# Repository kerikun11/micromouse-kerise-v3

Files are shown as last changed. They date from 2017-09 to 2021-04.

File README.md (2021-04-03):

# MicroMouse KERISE v3

ハーフサイズマイクロマウス

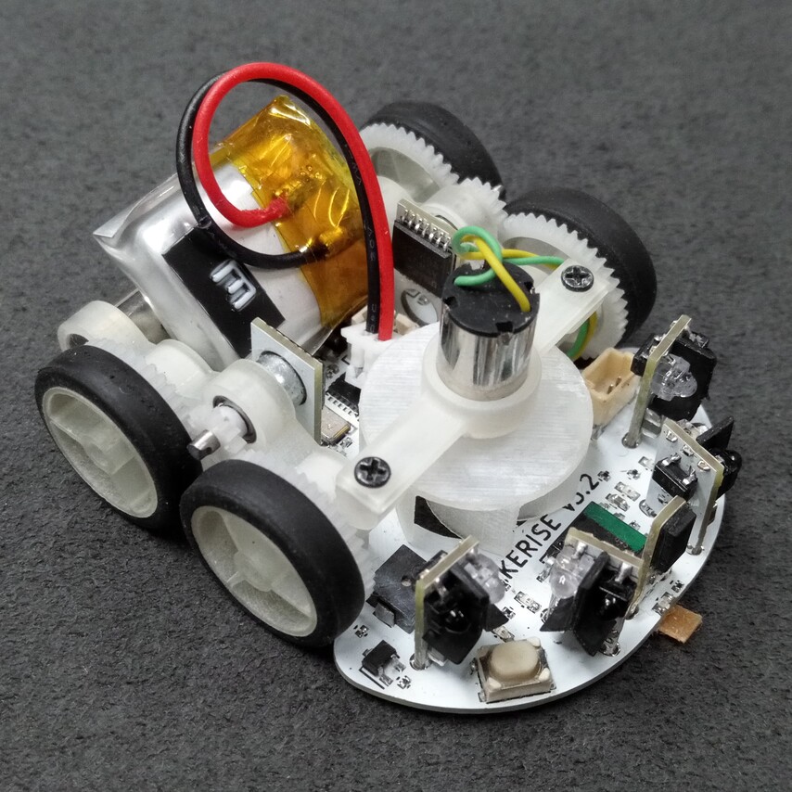
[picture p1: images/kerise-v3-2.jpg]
KERISE v3


## 戦績

- 第38回全日本マイクロマウス大会2017
  - ハーフサイズ競技エキスパートクラス予選13位
  - ハーフサイズ競技エキスパートクラス決勝13位
  - ハーフサイズ競技エキスパートクラス特別賞

## スペック

| 部品 | 型番 | 備考 |
| :--- | :--- | :--- |
| モーター | 不明 | 直径6mm 長さ10mm コアレスモーター |
| エンコーダ | AS5048A | 4096パルス 磁気式 |
| マイコン | ESP32-D0WD  | 240MHz dual core |
| 赤外線LED | VSMB294008G | 波長940mm |
| フォトダイオード | VEMD2020X01 | 波長940nm |
| モータードライバ | DRV8835 | 最大電流1.5A x 2ch |
| 6軸センサ | ICM-20602 | 3軸ジャイロ+3軸加速度 |
| バッテリー | 不明 | 3.7V 25C 100mAh 1S |

## 回路設計

- KiCad

## 開発環境

- ESP-IDF

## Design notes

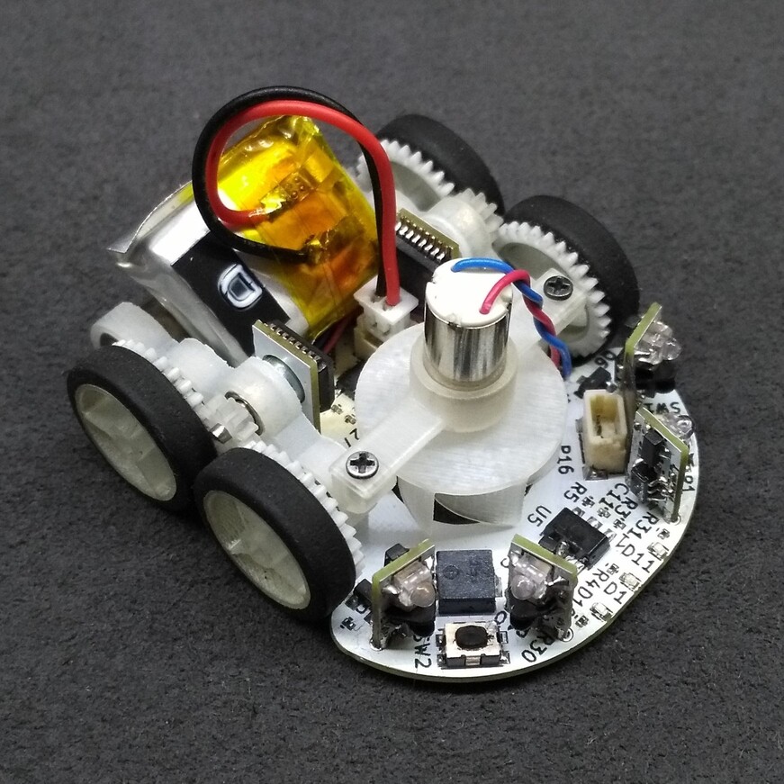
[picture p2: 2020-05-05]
images/kerise-v3-1.jpg

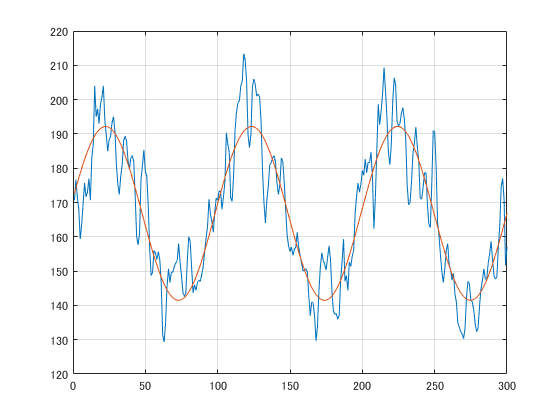
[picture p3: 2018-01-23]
matlab/fit.png

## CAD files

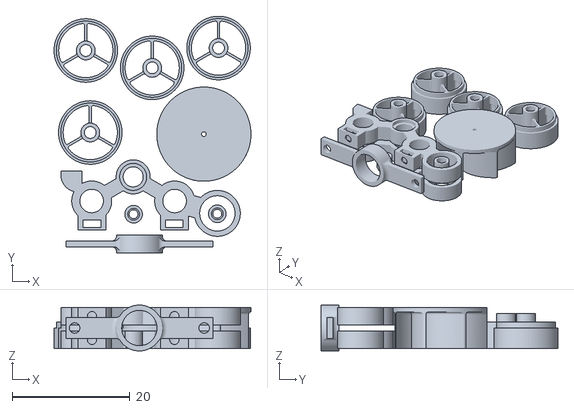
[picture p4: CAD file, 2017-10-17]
fusion360/print/main v1.stl
33.5 x 40.2 x 7.80

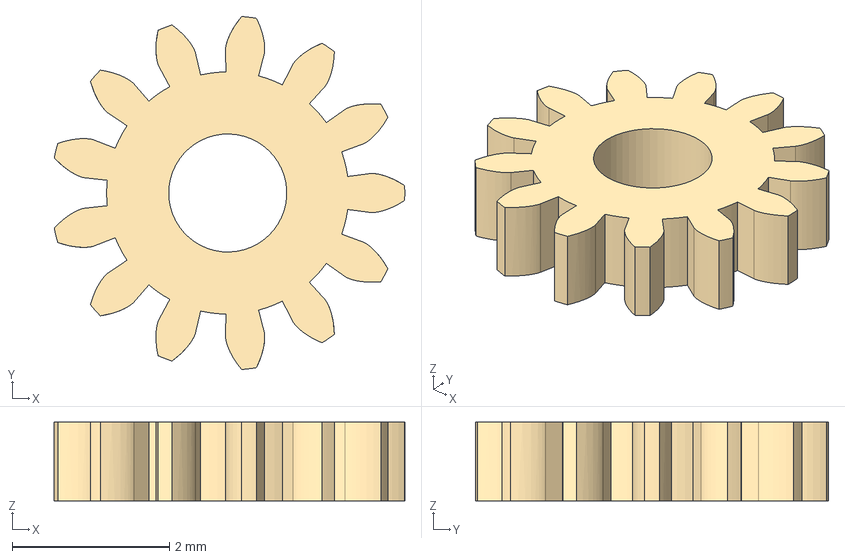
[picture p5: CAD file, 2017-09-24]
fusion360/gear/13.stp
4.46 x 4.49 x 1.00 mm

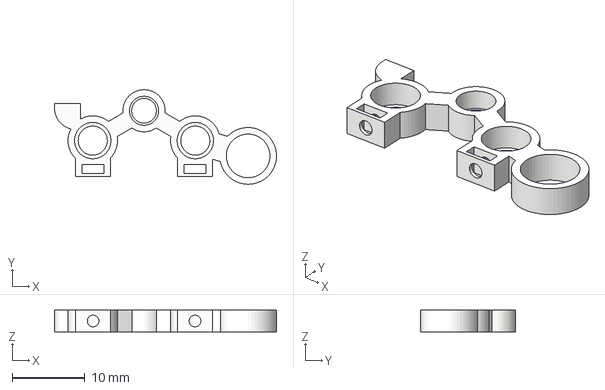
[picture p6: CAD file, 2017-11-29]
fusion360/parts/mounter v11.step
30.5 x 13.0 x 3.00 mm

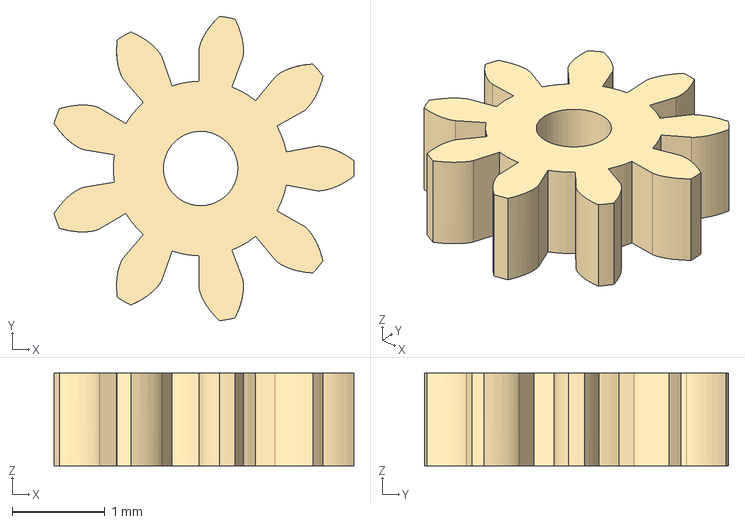
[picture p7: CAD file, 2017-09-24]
fusion360/gear/9.stp
3.23 x 3.28 x 1.00 mm

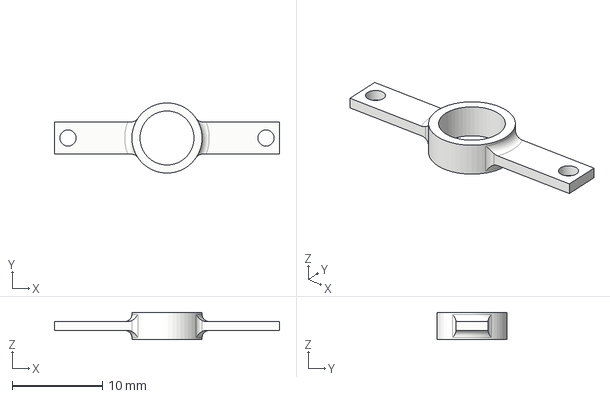
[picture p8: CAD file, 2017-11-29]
fusion360/parts/fan-mounter v1.step
25.0 x 7.80 x 3.00 mm

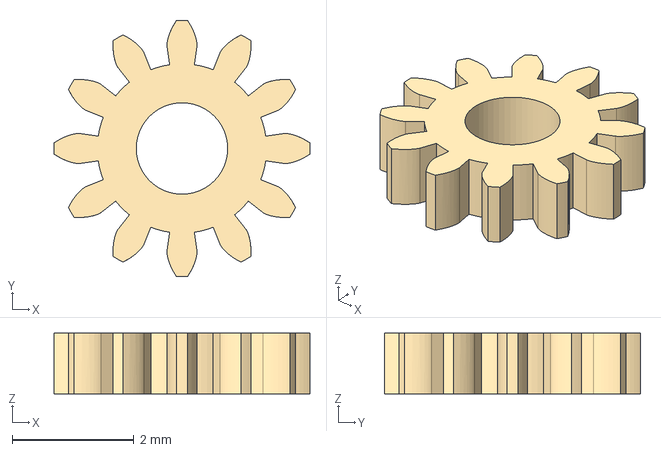
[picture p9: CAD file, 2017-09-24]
fusion360/gear/12.stp
4.20 x 4.20 x 1.00 mm

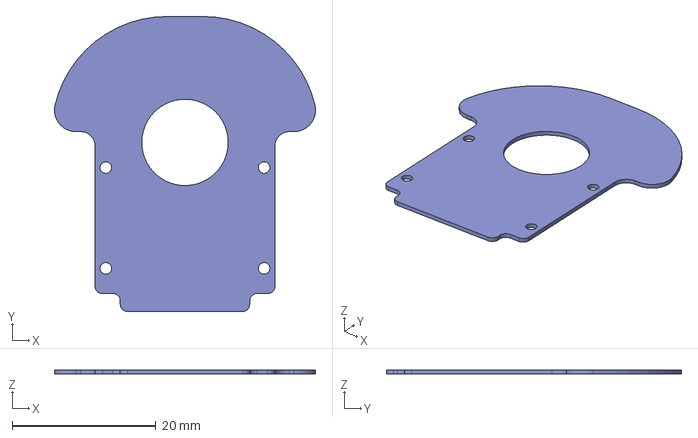
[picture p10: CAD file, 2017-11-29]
fusion360/parts/board v2.step
36.3 x 41.0 x 0.6 mm

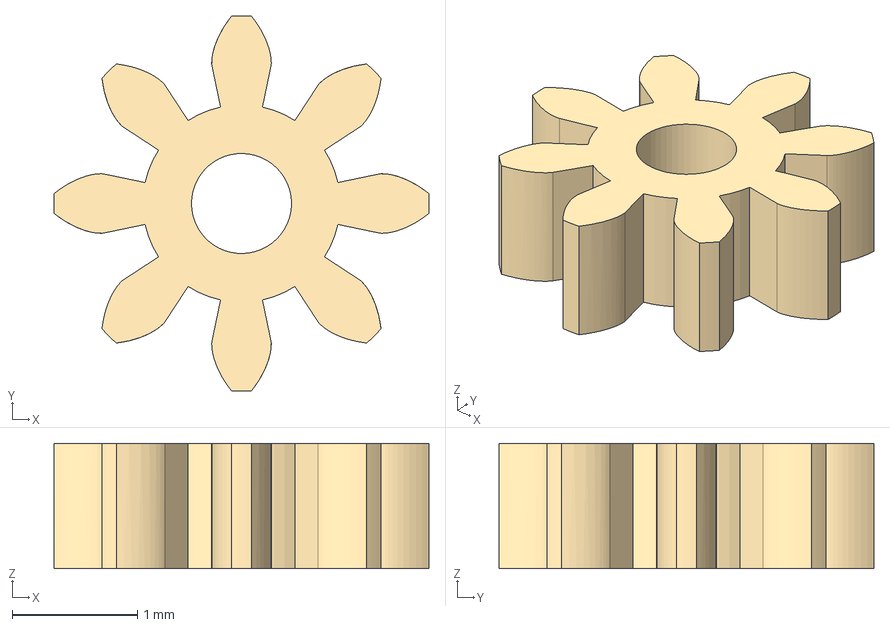
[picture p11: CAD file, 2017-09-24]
fusion360/gear/8.stp
3.00 x 3.00 x 1.00 mm

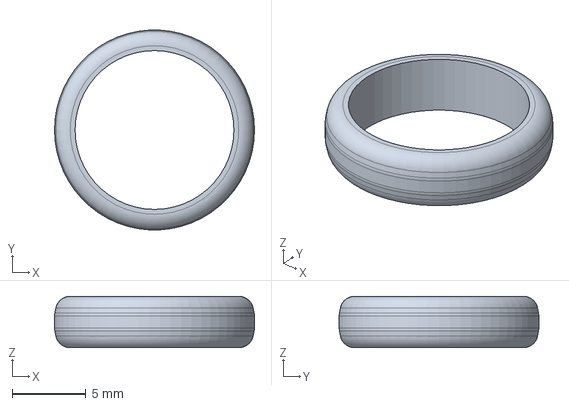
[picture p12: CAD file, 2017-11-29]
fusion360/parts/tire v1.step
13.6 x 13.6 x 3.50 mm

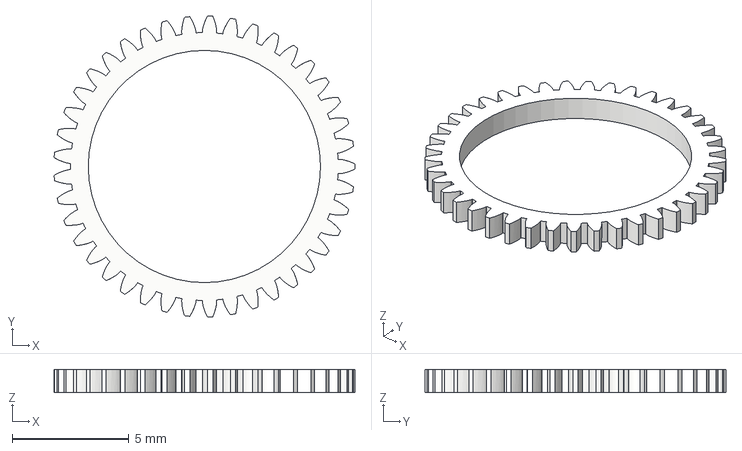
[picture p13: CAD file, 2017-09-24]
fusion360/gear/41.stp
12.9 x 12.9 x 1.00 mm

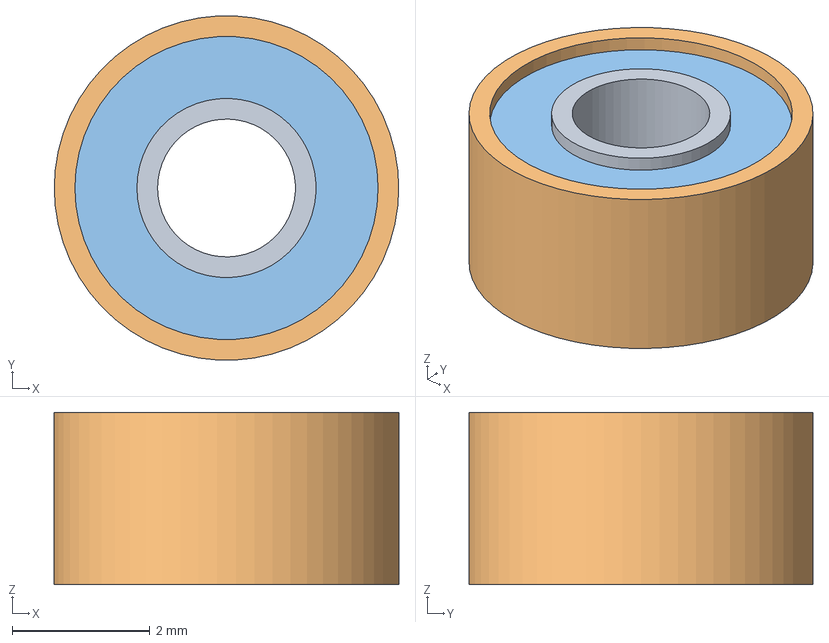
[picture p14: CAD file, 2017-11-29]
fusion360/parts/bearing_2_5_2.5 v1.step
5.00 x 4.99 x 2.50 mm

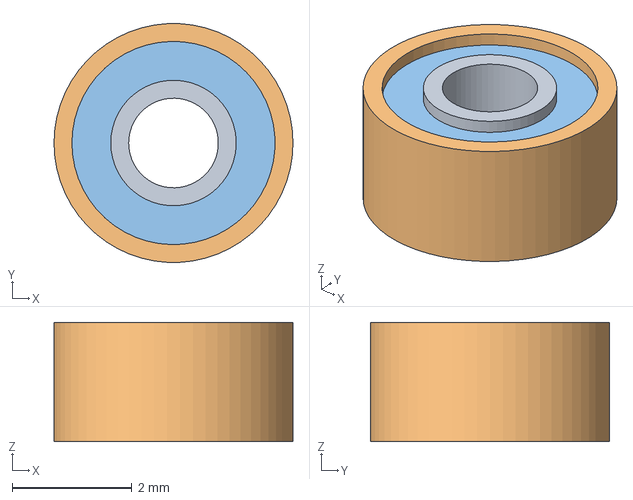
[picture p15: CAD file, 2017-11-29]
fusion360/parts/bearing_1.5_4_2 v1.step
4.00 x 3.99 x 2.00 mm

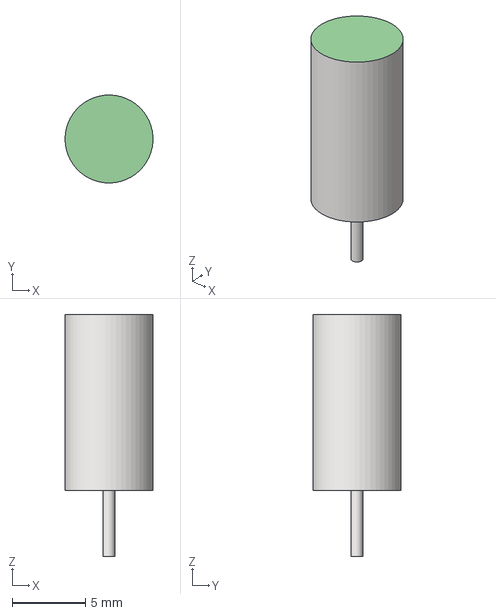
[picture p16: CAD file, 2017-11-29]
fusion360/parts/motor v1.step
5.99 x 6.00 x 16.5 mm

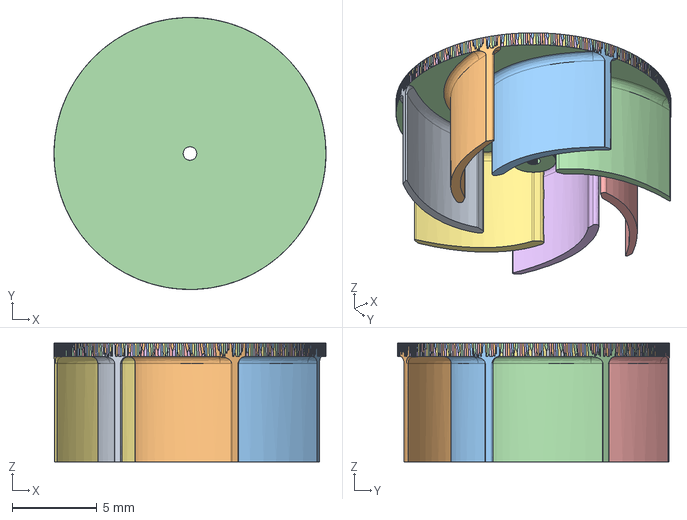
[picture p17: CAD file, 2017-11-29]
fusion360/parts/fan6 v1.step
16.0 x 16.0 x 7.00 mm

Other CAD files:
fusion360/parts/wheel v1.step
fusion360/parts/gear-pinion-9 v1.step
fusion360/parts/magnet-mounter v1.step
fusion360/parts/gear-wheel-41 v3.step
fusion360/gear/12.dxf
fusion360/gear/13.dxf
fusion360/gear/41.dxf
fusion360/gear/8.dxf
fusion360/gear/9.dxf
fusion360/parts/bearing_1.5_4_2 v1.f3d
fusion360/parts/bearing_2_5_2.5 v1.f3d
fusion360/parts/board v2.f3d
fusion360/parts/fan-mounter v1.f3d
fusion360/parts/fan6 v1.f3d
fusion360/parts/gear-encoder-13 v1.f3d
fusion360/parts/gear-encoder-13 v1.step
fusion360/parts/gear-pinion-9 v1.f3d
fusion360/parts/gear-wheel-41 v3.f3d
fusion360/parts/magnet-mounter v1.f3d
fusion360/parts/motor v1.f3d
fusion360/parts/mounter v11.f3d
fusion360/parts/tire v1.f3d
fusion360/parts/wheel v1.f3d

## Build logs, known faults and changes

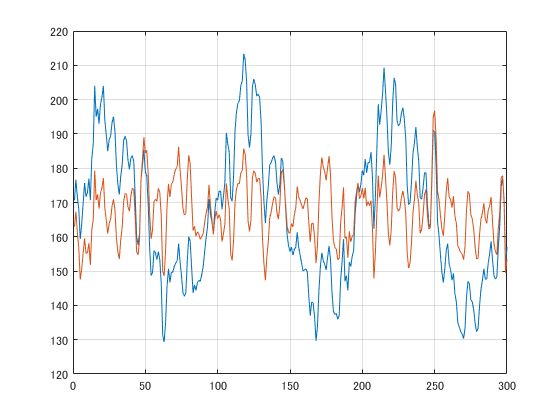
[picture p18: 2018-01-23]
matlab/fix.png

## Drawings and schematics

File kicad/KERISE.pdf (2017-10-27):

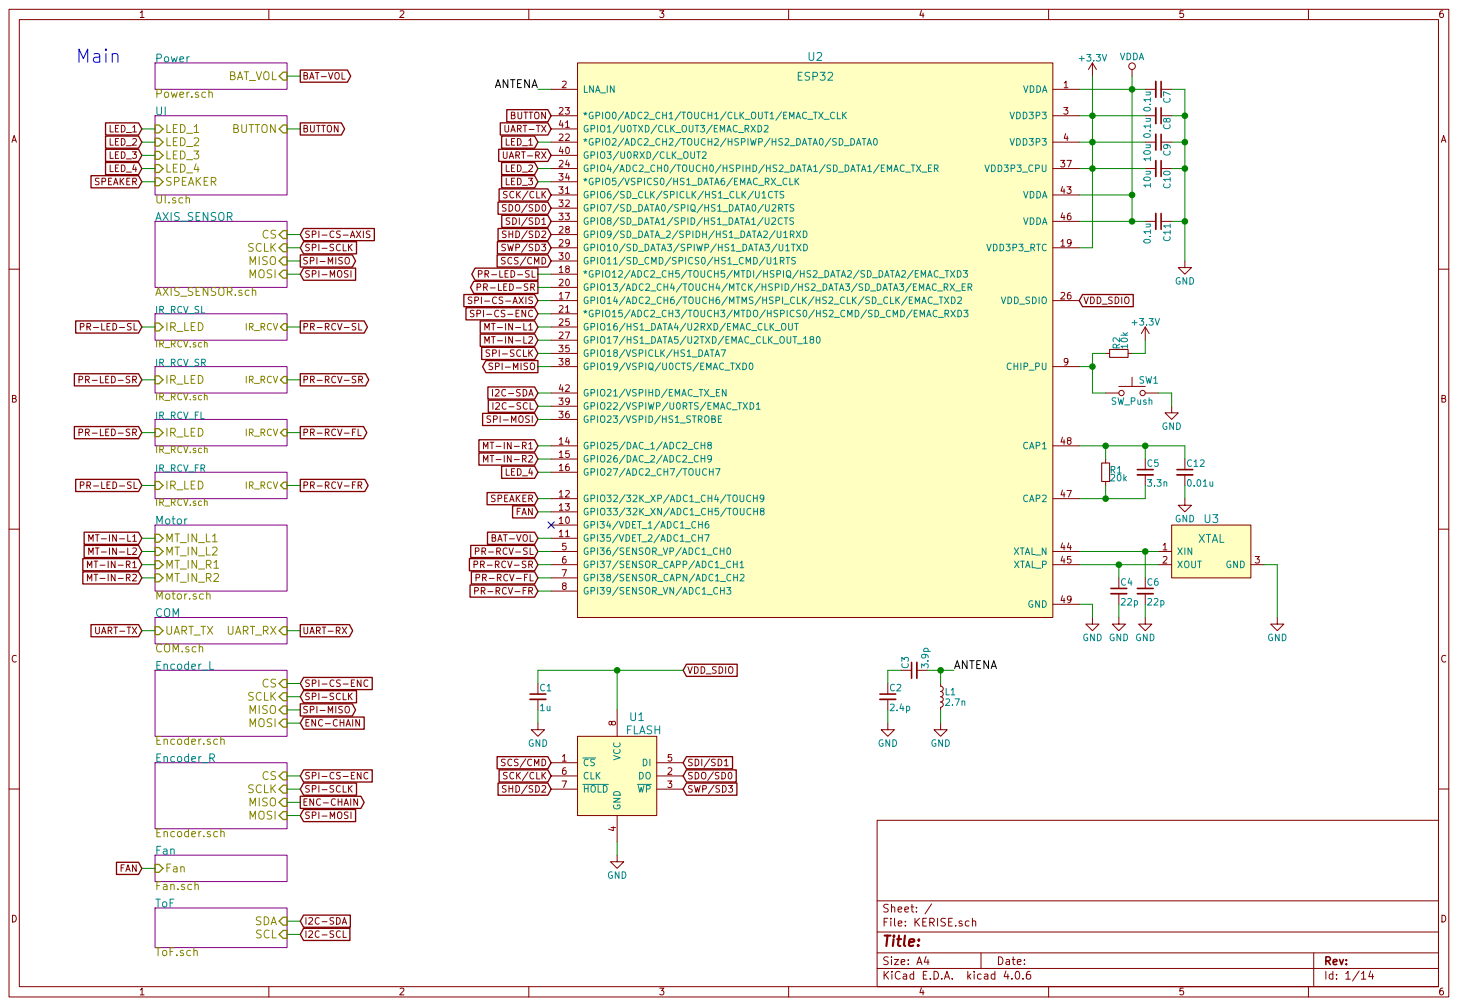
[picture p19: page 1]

BAT-VOL UI UI.sch SPEAKER

UART-TX UART-RX
LED_1

SW1 SW_Push PR-RCV-FL PR-RCV-FR

PR-RCV-FL PR-RCV-FR

UART_TX UART_RX
COM.sch
SPI-MOSI SPI-CS-ENC
SPI-SCLK

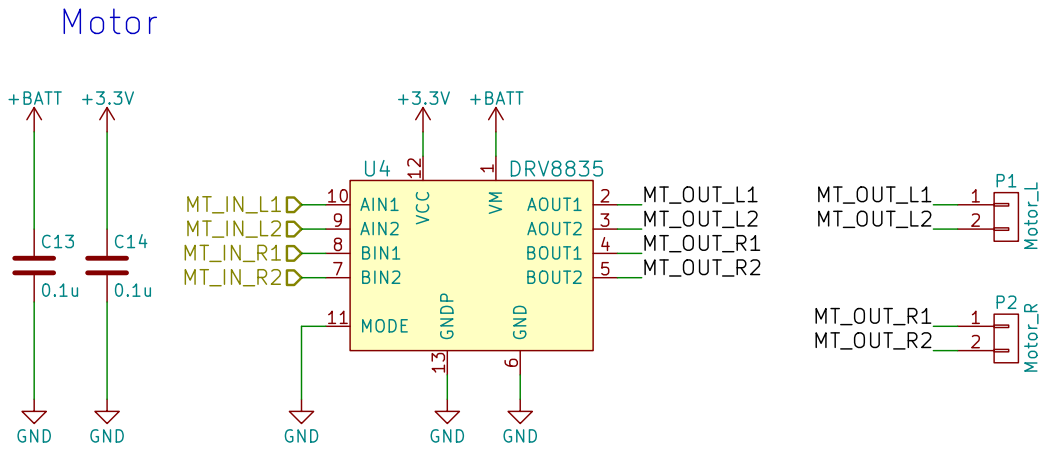
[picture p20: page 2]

6 BIN2 7 BIN1 8 AIN2 9 AIN1 10 MODE 11 VCC 12 GNDP 13 U4 DRV8835 GND GND GND MT_OUT_L1

1 AOUT1 2 AOUT2 3 BOUT1 4 BOUT2 5 GND
Id: 2/14 Title: File: Motor.sch Sheet: /Motor/ VM

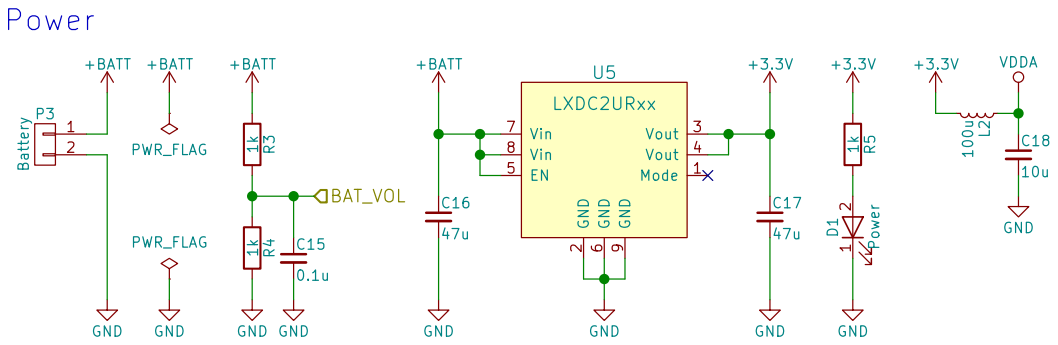
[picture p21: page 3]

2 Vout 3 Vout 4 EN 5 GND

Id: 3/14 Title: File: Power.sch Sheet: /Power/

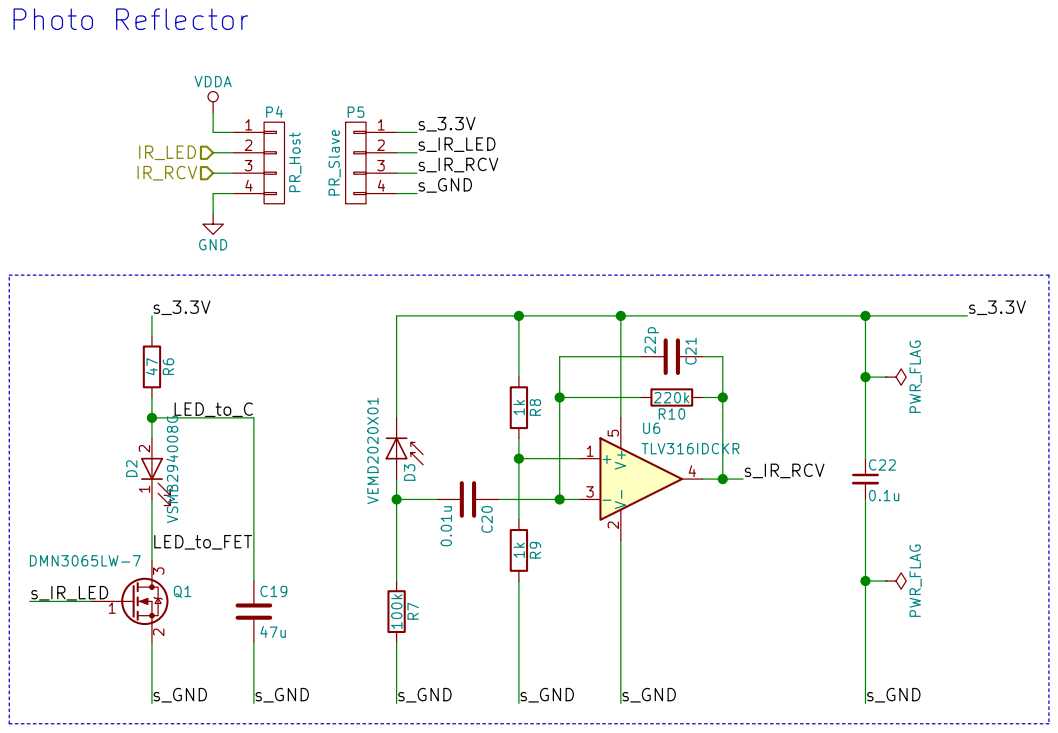
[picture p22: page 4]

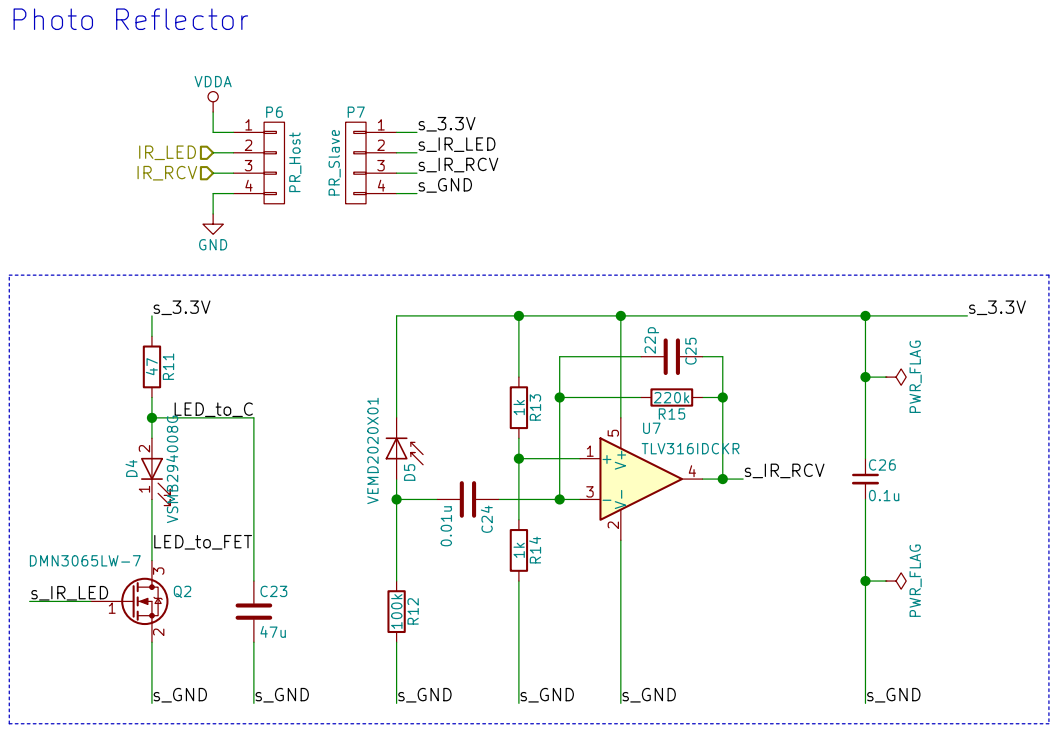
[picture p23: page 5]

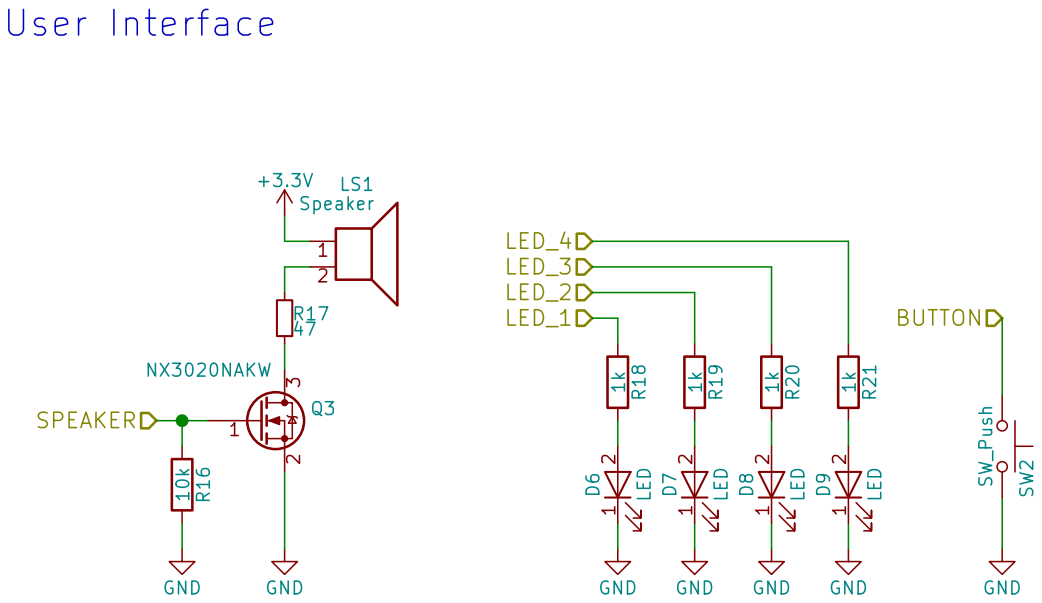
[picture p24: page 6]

Id: 6/14 Title: File: UI.sch Sheet: /UI/

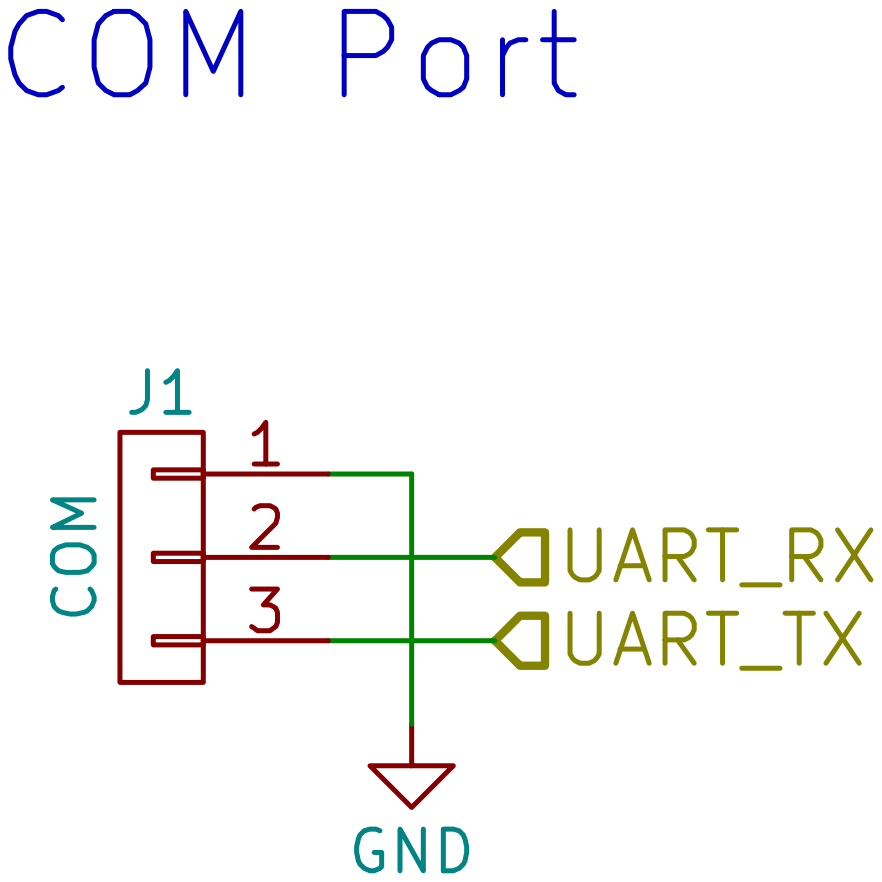
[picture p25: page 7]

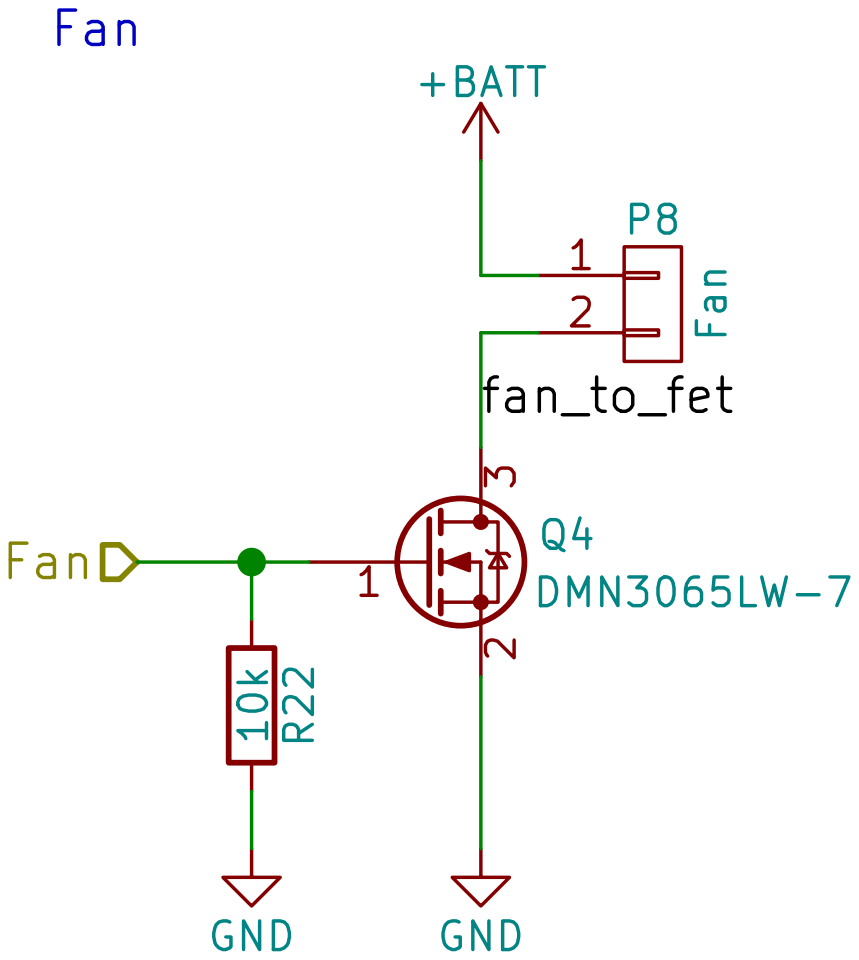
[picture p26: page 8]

Id: 8/14 Title: File: Fan.sch Sheet: /Fan/ 1

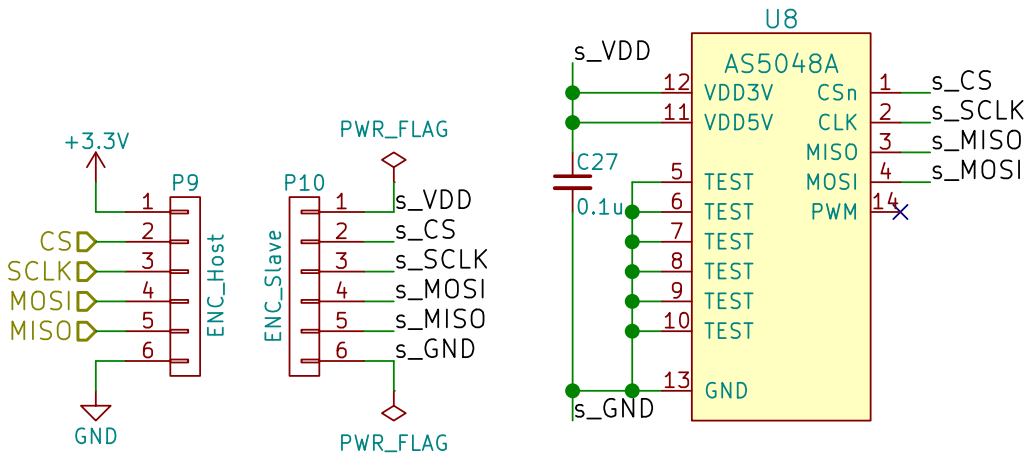
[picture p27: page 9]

Id: 9/14 Title: File: Encoder.sch Sheet: /Encoder_R/ GND CS

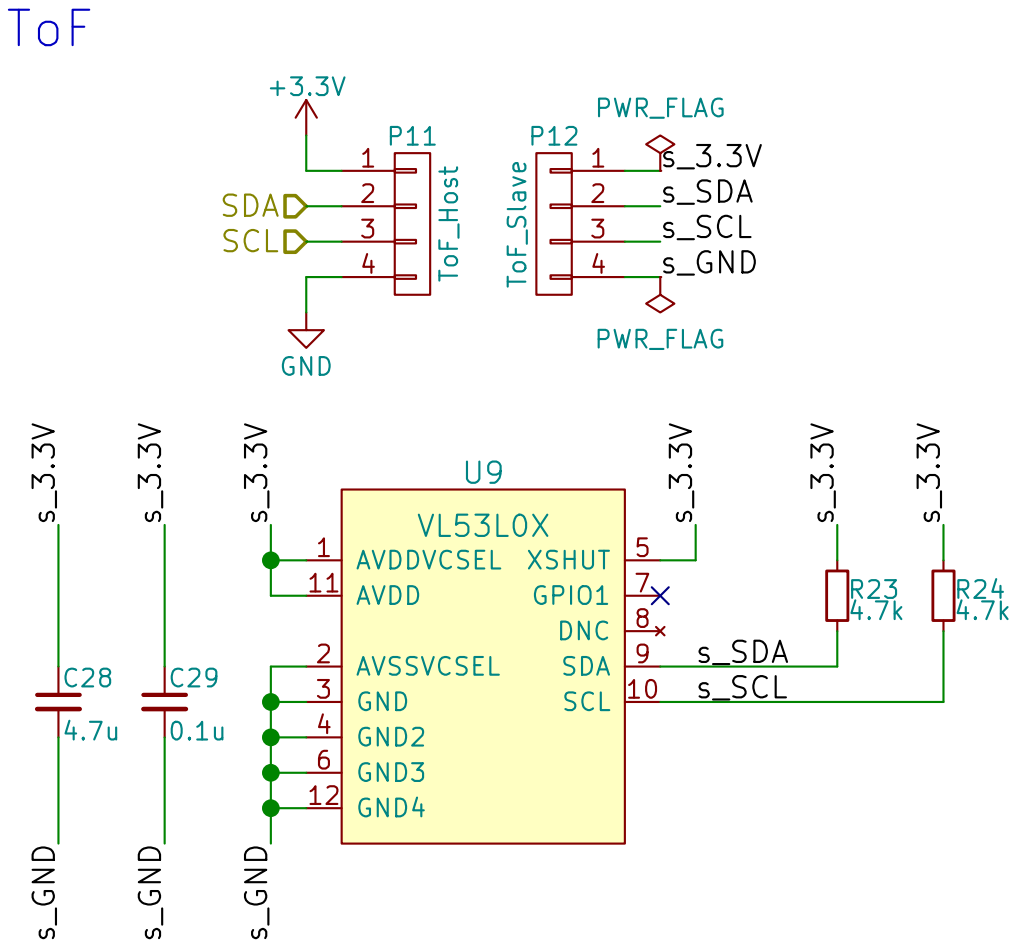
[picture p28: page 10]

Id: 10/14 Title: File: ToF.sch Sheet: /ToF/

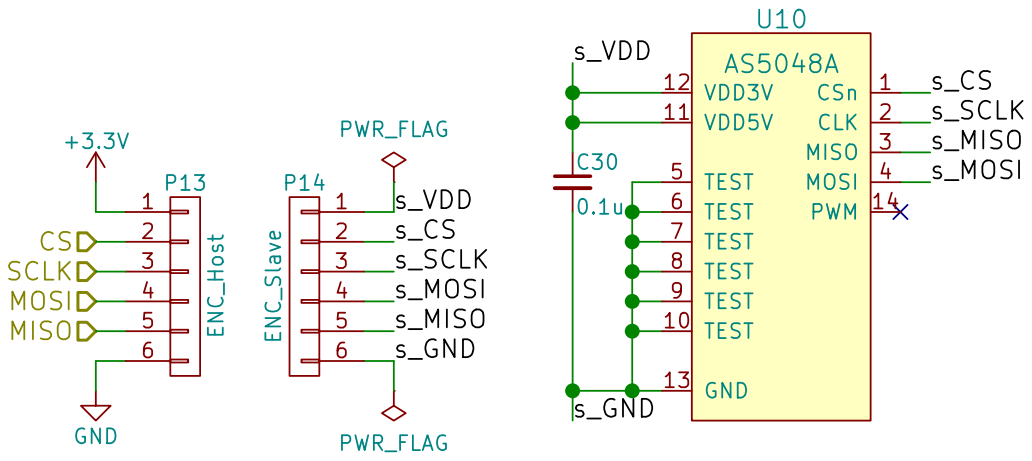
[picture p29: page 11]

Id: 11/14 Title: File: Encoder.sch Sheet: /Encoder_L/ GND CS

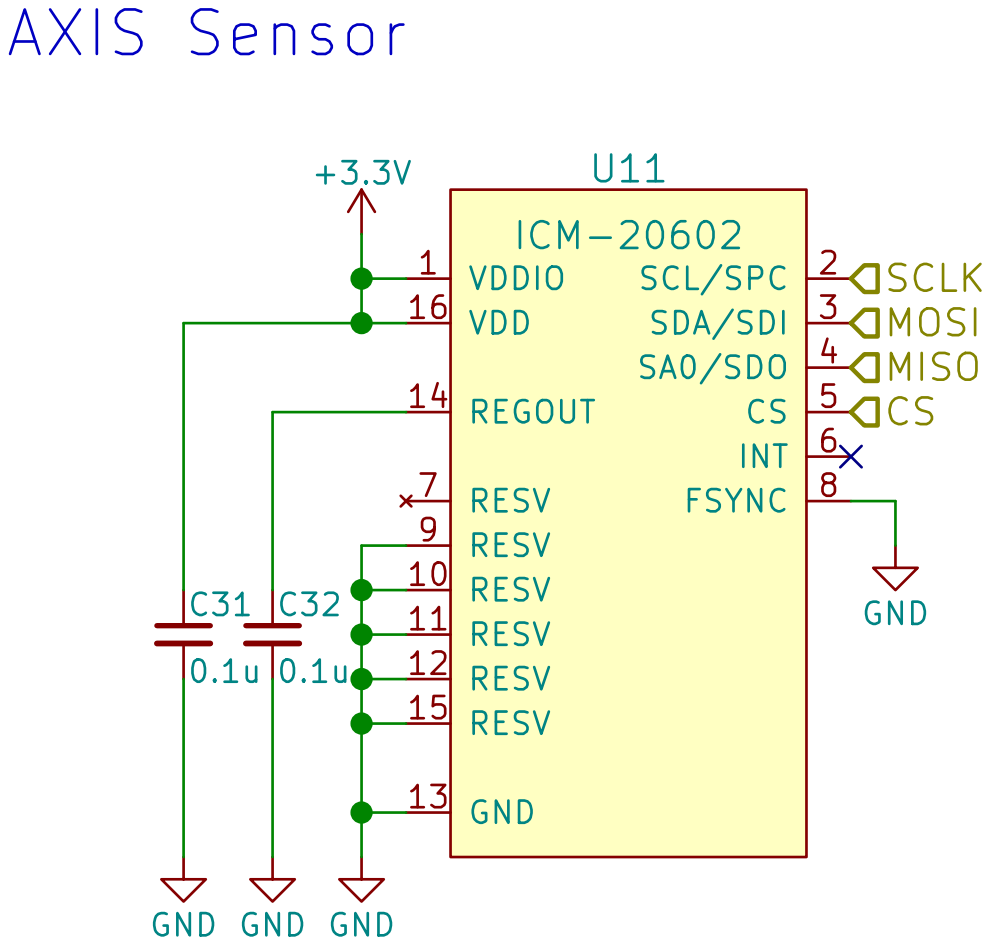
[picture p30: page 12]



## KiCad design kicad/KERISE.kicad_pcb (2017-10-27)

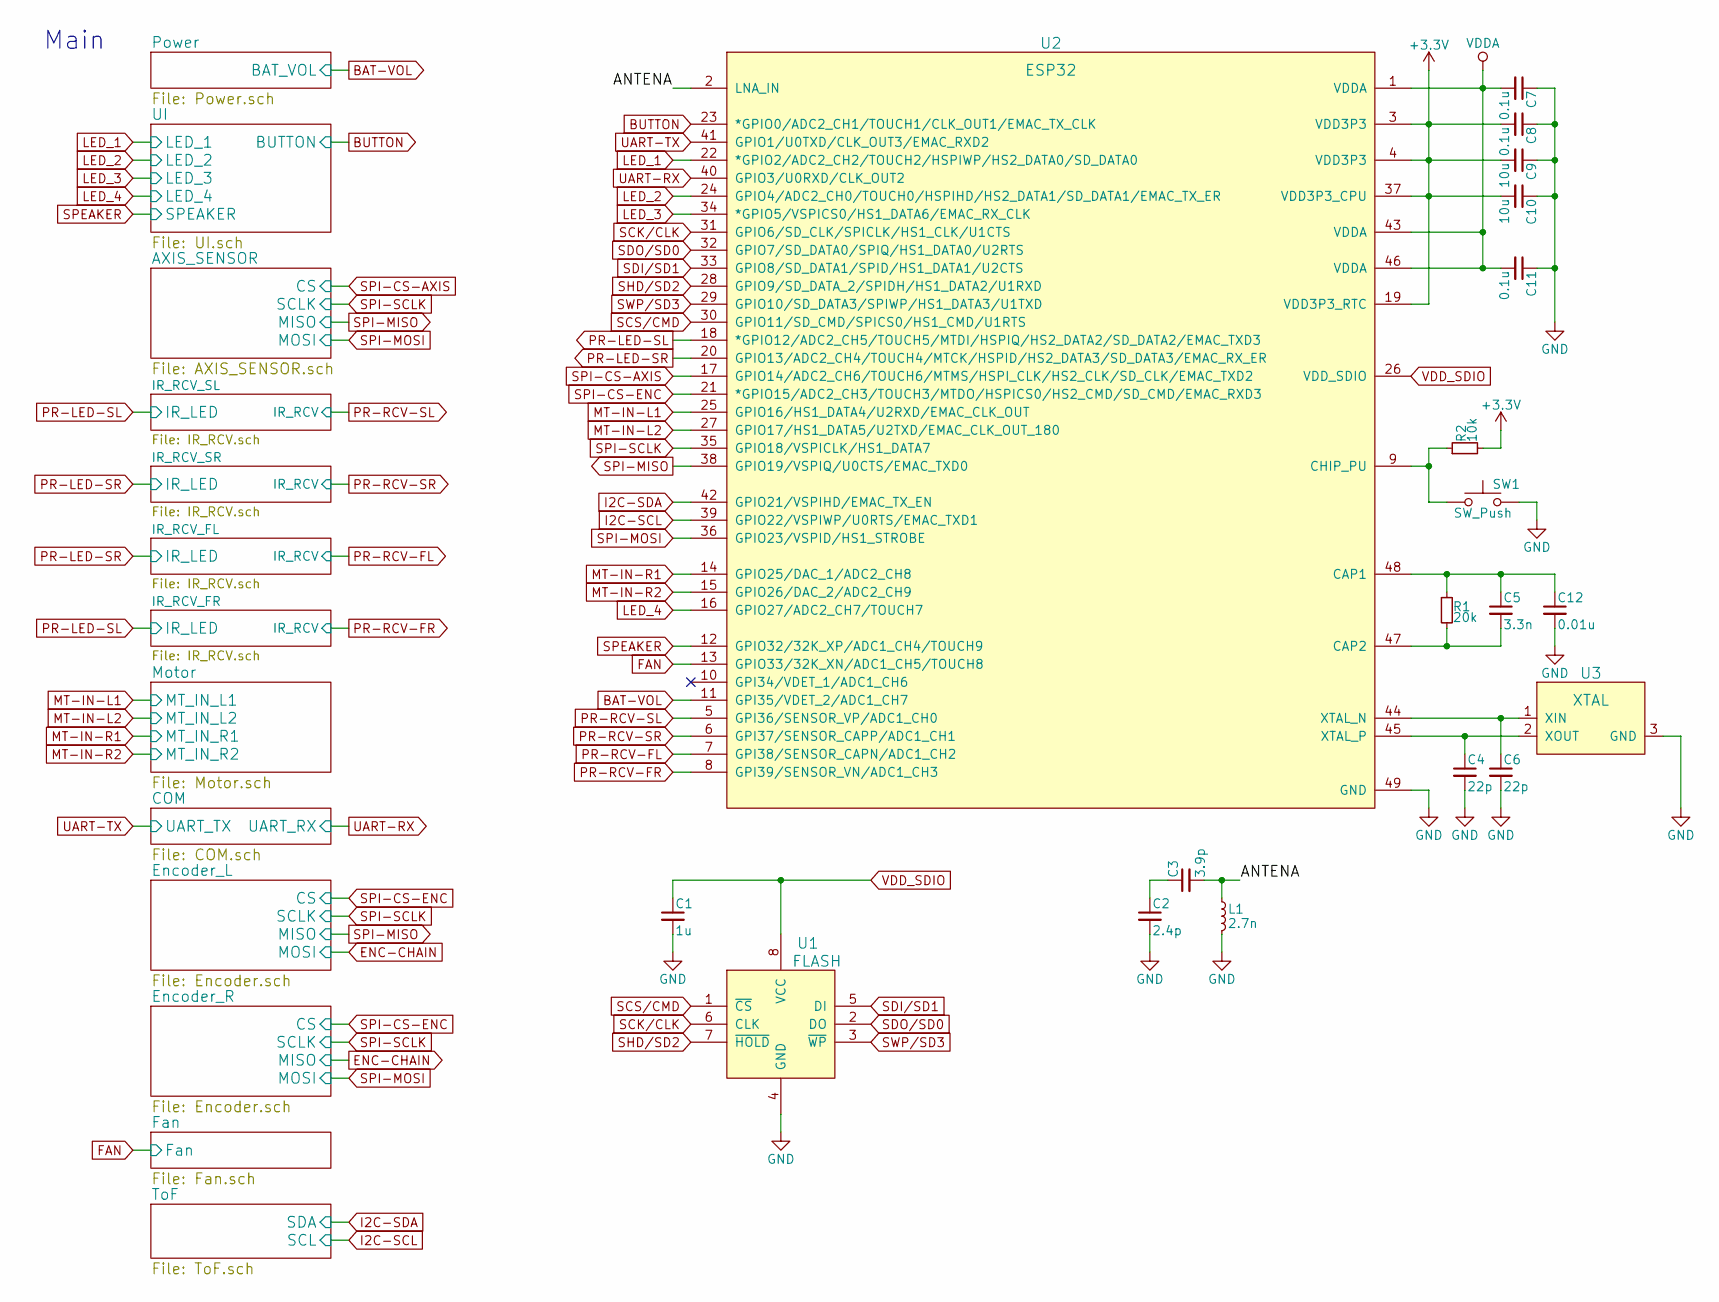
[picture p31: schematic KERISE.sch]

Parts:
C1: 1u; C_0402
C2: 2.4p; C_0201
C3: 3.9p; C_0201
C4, C6: 22p; C_0201
C5: 3.3n; C_0201
C7, C8, C11: 0.1u; C_0201
C9, C10: 10u; C_0402
C12: 0.01u; C_0201
L1: 2.7n; C_0201
R1: 20k; R_0201
R2: 10k; R_0201
SW1: SW_Push; SW_PUSH
U1: FLASH; SOIJ-8_5.3x5.3mm_Pitch1.27mm
U2: ESP32
U3: XTAL; crystal_FA238-TSX3225

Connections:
+3V3: C8.2, C9.2, C10.2, R2.2, U2.3 (VDD3P3), U2.4 (VDD3P3), U2.19 (VDD3P3_RTC), U2.37 (VDD3P3_CPU); also elsewhere on the board
/ANTENA: C3.2, L1.1, U2.2 (LNA_IN)
BAT-VOL: U2.11 (GPI35/VDET_2/ADC1_CH7); also elsewhere on the board
BUTTON: U2.23 (*GPIO0/ADC2_CH1/TOUCH1/CLK_OUT1/EMAC_TX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); also elsewhere on the board
FAN: U2.13 (GPIO33/32K_XN/ADC1_CH5/TOUCH8); also elsewhere on the board
GND: C1.2, C2.2, C4.2, C6.2, C7.1, C8.1, C9.1, C10.1, C11.1, C12.2, L1.2, SW1.2, U1.4 (GND), U2.49 (GND), U3.3 (GND); also elsewhere on the board
I2C-SCL: U2.39 (GPIO22/VSPIWP/U0RTS/EMAC_TXD1); also elsewhere on the board
I2C-SDA: U2.42 (GPIO21/VSPIHD/EMAC_TX_EN); also elsewhere on the board
LED_1: U2.22 (*GPIO2/ADC2_CH2/TOUCH2/HSPIWP/HS2_DATA0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); also elsewhere on the board
LED_2: U2.24 (GPIO4/ADC2_CH0/TOUCH0/HSPIHD/HS2_DATA1/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); also elsewhere on the board
LED_3: U2.34 (*GPIO5/VSPICS0/HS1_DATA6/EMAC_RX_CLK); also elsewhere on the board
LED_4: U2.16 (GPIO27/ADC2_CH7/TOUCH7); also elsewhere on the board
MT-IN-L1: U2.25 (GPIO16/HS1_DATA4/U2RXD/EMAC_CLK_OUT); also elsewhere on the board
MT-IN-L2: U2.27 (GPIO17/HS1_DATA5/U2TXD/EMAC_CLK_OUT_180); also elsewhere on the board
MT-IN-R1: U2.14 (GPIO25/DAC_1/ADC2_CH8); also elsewhere on the board
MT-IN-R2: U2.15 (GPIO26/DAC_2/ADC2_CH9); also elsewhere on the board
unnamed: C2.1, C3.1
unnamed: C4.1, U2.45 (XTAL_P), U3.2 (XOUT)
unnamed: C5.2, R1.2, U2.47 (CAP2)
unnamed: C6.1, U2.44 (XTAL_N), U3.1 (XIN)
unnamed: C5.1, C12.1, R1.1, U2.48 (CAP1)
unnamed: R2.1, SW1.1, U2.9 (CHIP_PU)
PR-LED-SL: U2.18 (*GPIO12/ADC2_CH5/TOUCH5/MTDI/HSPIQ/HS2_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); also elsewhere on the board
PR-LED-SR: U2.20 (GPIO13/ADC2_CH4/TOUCH4/MTCK/HSPID/HS2_D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); also elsewhere on the board
PR-RCV-FL: U2.7 (GPI38/SENSOR_CAPN/ADC1_CH2); also elsewhere on the board
PR-RCV-FR: U2.8 (GPI39/SENSOR_VN/ADC1_CH3); also elsewhere on the board
PR-RCV-SL: U2.5 (GPI36/SENSOR_VP/ADC1_CH0); also elsewhere on the board
PR-RCV-SR: U2.6 (GPI37/SENSOR_CAPP/ADC1_CH1); also elsewhere on the board
SCK/CLK: U1.6 (CLK), U2.31 (GPIO6/SD_CLK/SPICLK/HS1_CLK/U1CTS)
SCS/CMD: U1.1 (~CS), U2.30 (GPIO11/SD_CMD/SPICS0/HS1_CMD/U1RTS)
SDI/SD1: U1.5 (DI), U2.33 (GPIO8/SD_DATA1/SPID/HS1_DATA1/U2CTS)
SDO/SD0: U1.2 (DO), U2.32 (GPIO7/SD_DATA0/SPIQ/HS1_DATA0/U2RTS)
SHD/SD2: U1.7 (~HOLD), U2.28 (GPIO9/SD_DATA_2/SPIDH/HS1_DATA2/U1RXD)
SPEAKER: U2.12 (GPIO32/32K_XP/ADC1_CH4/TOUCH9); also elsewhere on the board
SPI-CS-AXIS: U2.17 (GPIO14/ADC2_CH6/TOUCH6/MTMS/HSPI_CLK/HS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); also elsewhere on the board
SPI-CS-ENC: U2.21 (*GPIO15/ADC2_CH3/TOUCH3/MTDO/HSPICS0/HS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); also elsewhere on the board
SPI-MISO: U2.38 (GPIO19/VSPIQ/U0CTS/EMAC_TXD0); also elsewhere on the board
SPI-MOSI: U2.36 (GPIO23/VSPID/HS1_STROBE); also elsewhere on the board
SPI-SCLK: U2.35 (GPIO18/VSPICLK/HS1_DATA7); also elsewhere on the board
SWP/SD3: U1.3 (~WP), U2.29 (GPIO10/SD_DATA3/SPIWP/HS1_DATA3/U1TXD)
UART-RX: U2.40 (GPIO3/U0RXD/CLK_OUT2); also elsewhere on the board
UART-TX: U2.41 (GPIO1/U0TXD/CLK_OUT3/EMAC_RXD2); also elsewhere on the board
VDDA: C7.2, C11.2, U2.1 (VDDA), U2.43 (VDDA), U2.46 (VDDA); also elsewhere on the board
VDD_SDIO: C1.1, U1.8 (VCC), U2.26 (VDD_SDIO)

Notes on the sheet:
Main

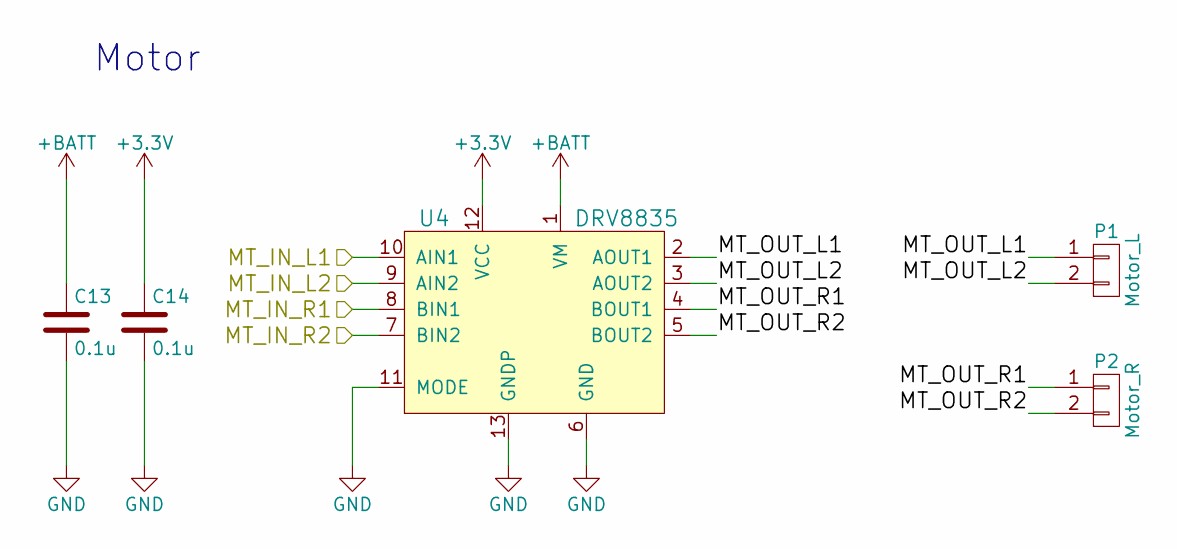
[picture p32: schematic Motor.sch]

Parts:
C13, C14: 0.1u; C_0201
P1: Motor_L; SMD_conn_2
P2: Motor_R; SMD_conn_2
U4: DRV8835

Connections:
+3V3: C14.1, U4.12 (VCC); also elsewhere on the board
+BATT: C13.1, U4.1 (VM); also elsewhere on the board
/Motor/MT_OUT_L1: P1.1, U4.2 (AOUT1)
/Motor/MT_OUT_L2: P1.2, U4.3 (AOUT2)
/Motor/MT_OUT_R1: P2.1, U4.4 (BOUT1)
/Motor/MT_OUT_R2: P2.2, U4.5 (BOUT2)
GND: C13.2, C14.2, U4.6 (GND), U4.11 (MODE), U4.13 (GNDP); also elsewhere on the board
MT-IN-L1: U4.10 (AIN1); also elsewhere on the board
MT-IN-L2: U4.9 (AIN2); also elsewhere on the board
MT-IN-R1: U4.8 (BIN1); also elsewhere on the board
MT-IN-R2: U4.7 (BIN2); also elsewhere on the board

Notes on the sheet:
Motor

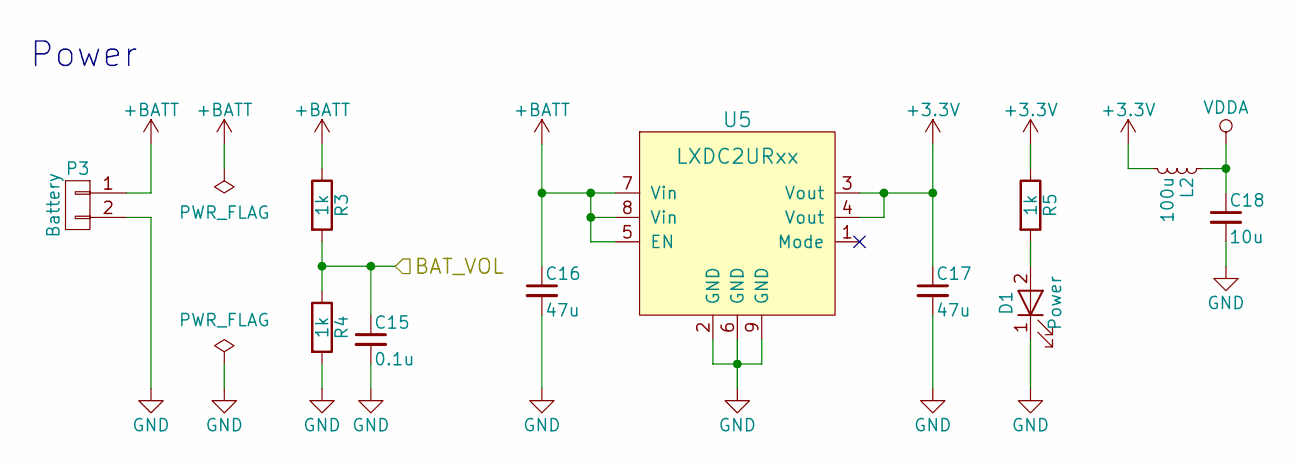
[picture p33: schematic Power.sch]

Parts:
C15: 0.1u; C_0201
C16, C17: 47u; C_0805
C18: 10u; C_0402
D1: Power; LED_0402
L2: 100u; C_0603
P3: Battery; Hirose_DF13-02P-1.25DSA_02x1.25mm_Straight
R3, R4, R5: 1k; R_0201
U5: LXDC2URxx; LXDC2UR

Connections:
+3V3: C17.1, L2.2, R5.1, U5.3 (Vout), U5.4 (Vout); also elsewhere on the board
+BATT: C16.1, P3.1, R3.1, U5.5 (EN), U5.7 (Vin), U5.8 (Vin); also elsewhere on the board
BAT-VOL: C15.1, R3.2, R4.1; also elsewhere on the board
GND: C15.2, C16.2, C17.2, C18.2, D1.1 (K), P3.2, R4.2, U5.2 (GND), U5.6 (GND), U5.9 (GND); also elsewhere on the board
unnamed: D1.2 (A), R5.2
VDDA: C18.1, L2.1; also elsewhere on the board

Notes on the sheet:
Power

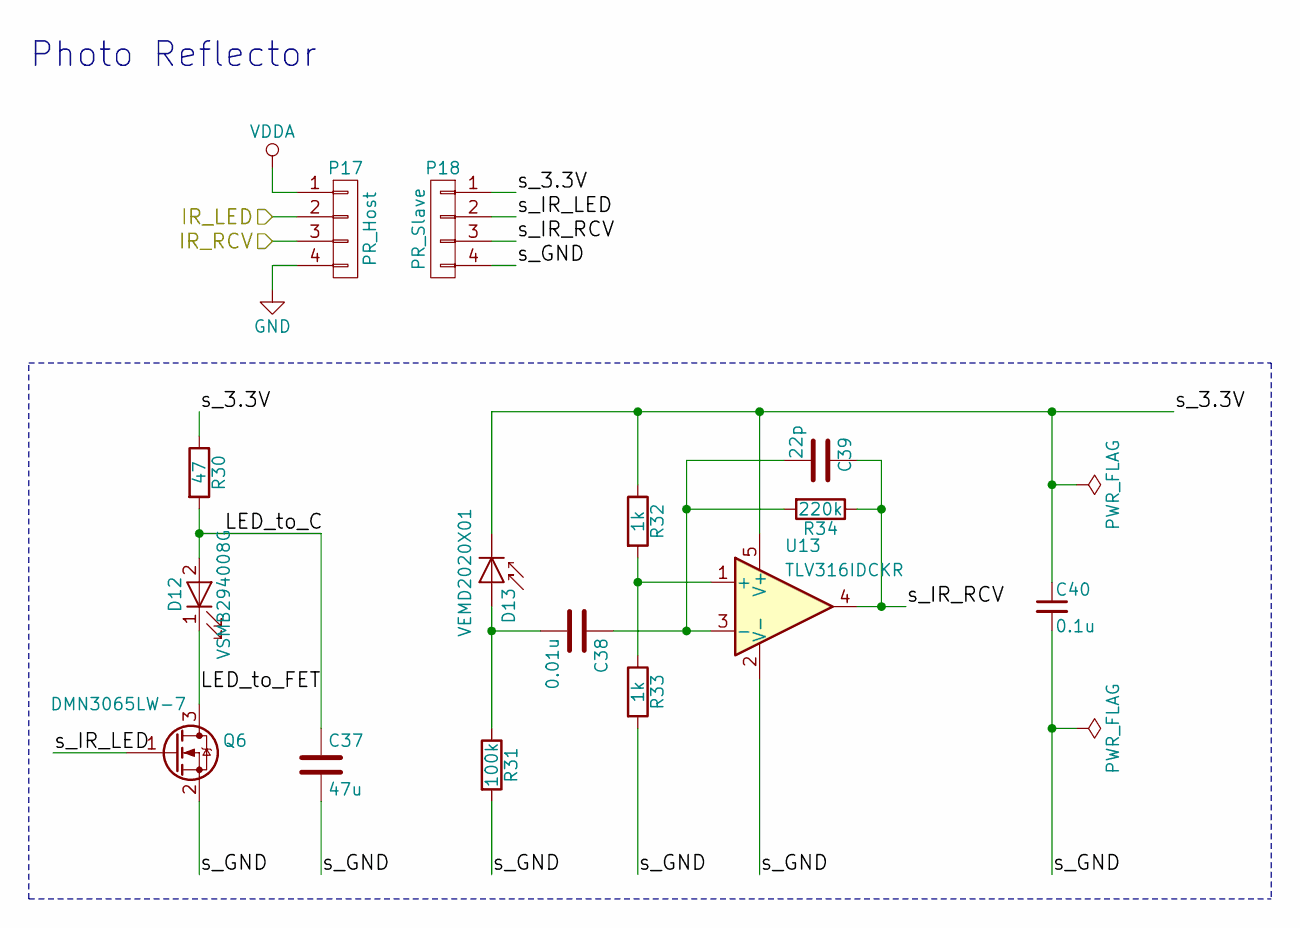
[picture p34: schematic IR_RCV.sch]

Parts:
C19: 47u; C_0805
C20: 0.01u; C_0201
C21: 22p; C_0201
C22: 0.1u; C_0201
D2: VSMB294008G; VISHAY_DIODE
D3: VEMD2020X01; VISHAY_DIODE
P4: PR_Host; STAND_PR_HOST
P5: PR_Slave; STAND_PR_SLAVE
Q1: DMN3065LW-7; SOT-323_SC-70
R6: 47; R_0603
R7: 100k; R_0201
R8, R9: 1k; R_0201
R10: 220k; R_0201
U6: TLV316IDCKR; SOT-353_SC-70-5

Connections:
/IR_RCV_SL/LED_to_C: C19.1, D2.2 (A), R6.2
/IR_RCV_SL/LED_to_FET: D2.1 (K), Q1.3 (D)
/IR_RCV_SL/s_3.3V: C22.1, D3.1 (K), P5.1, R6.1, R8.1, U6.5 (V+)
/IR_RCV_SL/s_GND: C19.2, C22.2, P5.4, Q1.2 (S), R7.2, R9.2, U6.2 (V-)
/IR_RCV_SL/s_IR_LED: P5.2, Q1.1 (G)
/IR_RCV_SL/s_IR_RCV: C21.1, P5.3, R10.1, U6.4
GND: P4.4; also elsewhere on the board
unnamed: C20.1, C21.2, R10.2, U6.3 (-)
unnamed: C20.2, D3.2 (A), R7.1
unnamed: R8.2, R9.1, U6.1 (+)
PR-LED-SL: P4.2; also elsewhere on the board
PR-RCV-SL: P4.3; also elsewhere on the board
VDDA: P4.1; also elsewhere on the board

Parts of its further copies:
C23, C33, C37: 47u; C_0805
C24, C34, C38: 0.01u; C_0201
C25, C35, C39: 22p; C_0201
C26, C36, C40: 0.1u; C_0201
D4, D10, D12: VSMB294008G; VISHAY_DIODE
D5, D11, D13: VEMD2020X01; VISHAY_DIODE
P6, P15, P17: PR_Host; STAND_PR_HOST
P7, P16, P18: PR_Slave; STAND_PR_SLAVE
Q2, Q5, Q6: DMN3065LW-7; SOT-323_SC-70
R11, R25, R30: 47; R_0603
R12, R26, R31: 100k; R_0201
R13, R14, R27, R28, R32, R33: 1k; R_0201
R15, R29, R34: 220k; R_0201
U7, U12, U13: TLV316IDCKR; SOT-353_SC-70-5

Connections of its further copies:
/IR_RCV_FL/LED_to_C: C33.1, D10.2 (A), R25.2
/IR_RCV_FL/LED_to_FET: D10.1 (K), Q5.3 (D)
/IR_RCV_FL/s_3.3V: C36.1, D11.1 (K), P16.1, R25.1, R27.1, U12.5 (V+)
/IR_RCV_FL/s_GND: C33.2, C36.2, P16.4, Q5.2 (S), R26.2, R28.2, U12.2 (V-)
/IR_RCV_FL/s_IR_LED: P16.2, Q5.1 (G)
/IR_RCV_FL/s_IR_RCV: C35.1, P16.3, R29.1, U12.4
/IR_RCV_FR/LED_to_C: C37.1, D12.2 (A), R30.2
/IR_RCV_FR/LED_to_FET: D12.1 (K), Q6.3 (D)
/IR_RCV_FR/s_3.3V: C40.1, D13.1 (K), P18.1, R30.1, R32.1, U13.5 (V+)
/IR_RCV_FR/s_GND: C37.2, C40.2, P18.4, Q6.2 (S), R31.2, R33.2, U13.2 (V-)
/IR_RCV_FR/s_IR_LED: P18.2, Q6.1 (G)
/IR_RCV_FR/s_IR_RCV: C39.1, P18.3, R34.1, U13.4
/IR_RCV_SR/LED_to_C: C23.1, D4.2 (A), R11.2
/IR_RCV_SR/LED_to_FET: D4.1 (K), Q2.3 (D)
/IR_RCV_SR/s_3.3V: C26.1, D5.1 (K), P7.1, R11.1, R13.1, U7.5 (V+)
/IR_RCV_SR/s_GND: C23.2, C26.2, P7.4, Q2.2 (S), R12.2, R14.2, U7.2 (V-)
/IR_RCV_SR/s_IR_LED: P7.2, Q2.1 (G)
/IR_RCV_SR/s_IR_RCV: C25.1, P7.3, R15.1, U7.4
GND: P6.4, P15.4, P17.4; also elsewhere on the board
unnamed: C24.1, C25.2, R15.2, U7.3 (-)
unnamed: C24.2, D5.2 (A), R12.1
unnamed: C34.1, C35.2, R29.2, U12.3 (-)
unnamed: C34.2, D11.2 (A), R26.1
unnamed: C38.1, C39.2, R34.2, U13.3 (-)
unnamed: C38.2, D13.2 (A), R31.1
unnamed: R13.2, R14.1, U7.1 (+)
unnamed: R27.2, R28.1, U12.1 (+)
unnamed: R32.2, R33.1, U13.1 (+)
PR-LED-SL: P17.2; also elsewhere on the board
PR-LED-SR: P6.2, P15.2; also elsewhere on the board
PR-RCV-FL: P15.3; also elsewhere on the board
PR-RCV-FR: P17.3; also elsewhere on the board
PR-RCV-SR: P6.3; also elsewhere on the board
VDDA: P6.1, P15.1, P17.1; also elsewhere on the board

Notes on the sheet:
Photo Reflector

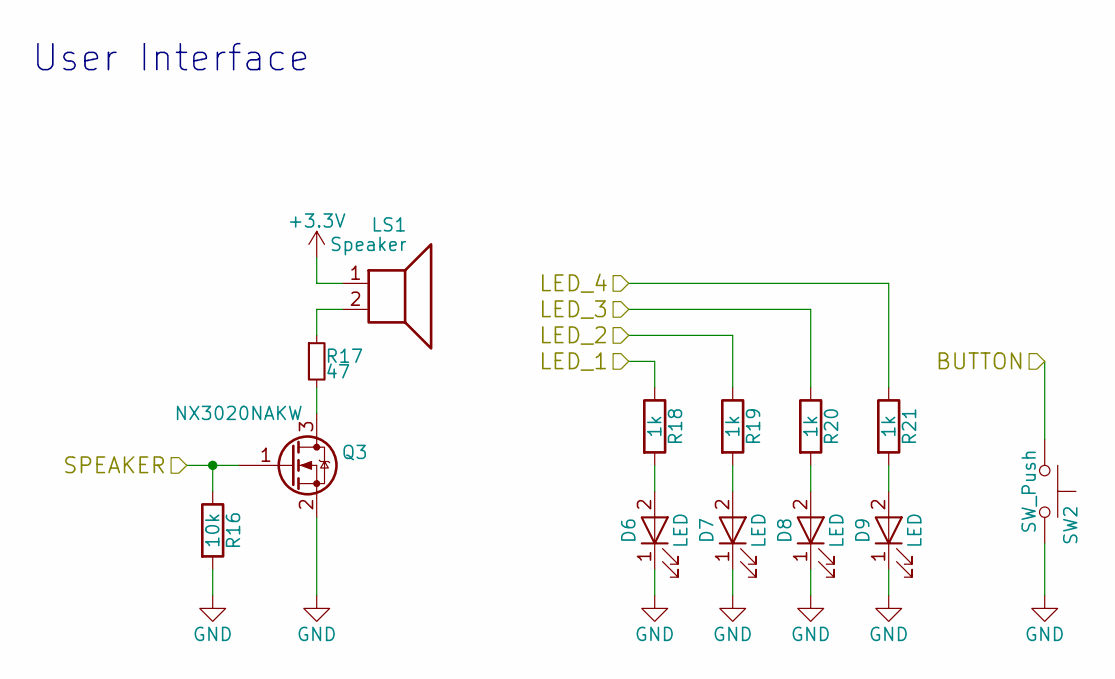
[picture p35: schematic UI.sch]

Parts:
D6, D7, D8, D9: LED; LED_0402
LS1: Speaker; SMT-0440-S-R
Q3: NX3020NAKW; SOT-323_SC-70
R16: 10k; R_0201
R17: 47; R_0201
R18, R19, R20, R21: 1k; R_0201
SW2: SW_Push; SW_PUSH

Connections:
+3V3: LS1.1; also elsewhere on the board
BUTTON: SW2.1; also elsewhere on the board
GND: D6.1 (K), D7.1 (K), D8.1 (K), D9.1 (K), Q3.2 (S), R16.2, SW2.2; also elsewhere on the board
LED_1: R18.1; also elsewhere on the board
LED_2: R19.1; also elsewhere on the board
LED_3: R20.1; also elsewhere on the board
LED_4: R21.1; also elsewhere on the board
unnamed: D6.2 (A), R18.2
unnamed: D7.2 (A), R19.2
unnamed: D8.2 (A), R20.2
unnamed: D9.2 (A), R21.2
unnamed: LS1.2, R17.1
unnamed: Q3.3 (D), R17.2
SPEAKER: Q3.1 (G), R16.1; also elsewhere on the board

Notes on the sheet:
User Interface

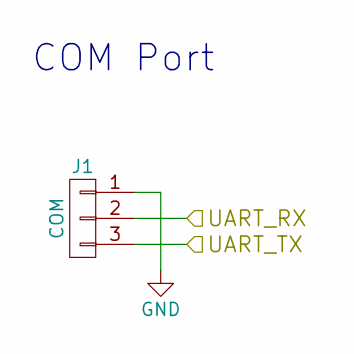
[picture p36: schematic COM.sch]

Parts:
J1: COM; JST_SH_BM03B-SRSS-TB_03x1.00mm_Straight

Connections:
GND: J1.1; also elsewhere on the board
UART-RX: J1.2; also elsewhere on the board
UART-TX: J1.3; also elsewhere on the board

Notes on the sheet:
COM Port

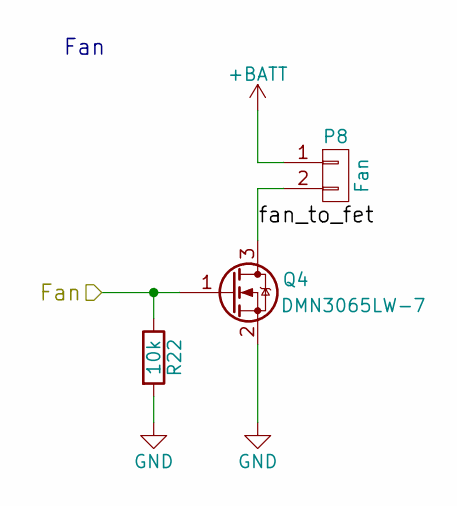
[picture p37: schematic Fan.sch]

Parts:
P8: Fan; SMD_conn_2
Q4: DMN3065LW-7; SOT-323_SC-70
R22: 10k; R_0201

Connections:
+BATT: P8.1; also elsewhere on the board
/Fan/fan_to_fet: P8.2, Q4.3 (D)
FAN: Q4.1 (G), R22.1; also elsewhere on the board
GND: Q4.2 (S), R22.2; also elsewhere on the board

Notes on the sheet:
Fan

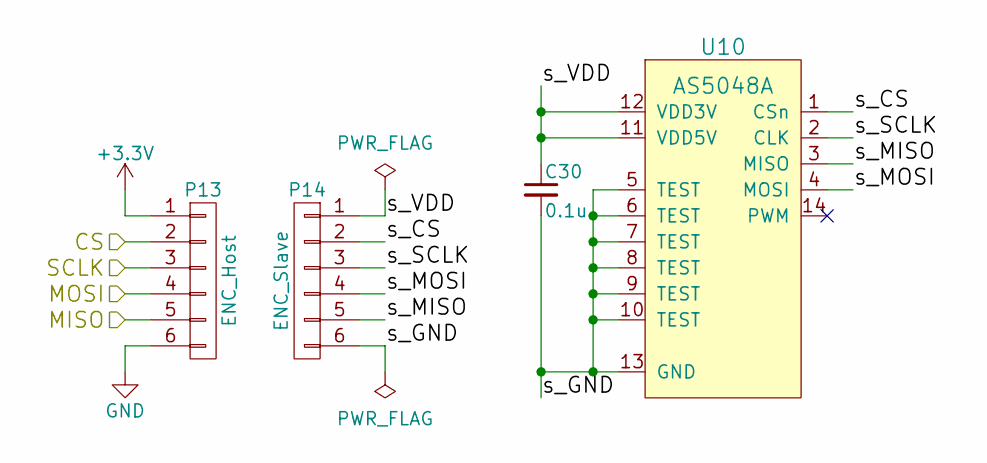
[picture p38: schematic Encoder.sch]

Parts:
C27: 0.1u; C_0201
P9: ENC_Host; STAND_AS_HOST
P10: ENC_Slave; STAND_AS_SLAVE
U8: AS5048A; TSSOP-14_4.4x5mm_Pitch0.65mm

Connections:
+3V3: P9.1; also elsewhere on the board
/Encoder_R/s_CS: P10.2, U8.1 (CSn)
/Encoder_R/s_GND: C27.2, P10.6, U8.5 (TEST), U8.6 (TEST), U8.7 (TEST), U8.8 (TEST), U8.9 (TEST), U8.10 (TEST), U8.13 (GND)
/Encoder_R/s_MISO: P10.5, U8.3 (MISO)
/Encoder_R/s_MOSI: P10.4, U8.4 (MOSI)
/Encoder_R/s_SCLK: P10.3, U8.2 (CLK)
/Encoder_R/s_VDD: C27.1, P10.1, U8.11 (VDD5V), U8.12 (VDD3V)
ENC-CHAIN: P9.5; also elsewhere on the board
GND: P9.6; also elsewhere on the board
SPI-CS-ENC: P9.2; also elsewhere on the board
SPI-MOSI: P9.4; also elsewhere on the board
SPI-SCLK: P9.3; also elsewhere on the board

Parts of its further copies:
C30: 0.1u; C_0201
P13: ENC_Host; STAND_AS_HOST
P14: ENC_Slave; STAND_AS_SLAVE
U10: AS5048A; TSSOP-14_4.4x5mm_Pitch0.65mm

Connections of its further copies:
+3V3: P13.1; also elsewhere on the board
/Encoder_L/s_CS: P14.2, U10.1 (CSn)
/Encoder_L/s_GND: C30.2, P14.6, U10.5 (TEST), U10.6 (TEST), U10.7 (TEST), U10.8 (TEST), U10.9 (TEST), U10.10 (TEST), U10.13 (GND)
/Encoder_L/s_MISO: P14.5, U10.3 (MISO)
/Encoder_L/s_MOSI: P14.4, U10.4 (MOSI)
/Encoder_L/s_SCLK: P14.3, U10.2 (CLK)
/Encoder_L/s_VDD: C30.1, P14.1, U10.11 (VDD5V), U10.12 (VDD3V)
ENC-CHAIN: P13.4; also elsewhere on the board
GND: P13.6; also elsewhere on the board
SPI-CS-ENC: P13.2; also elsewhere on the board
SPI-MISO: P13.5; also elsewhere on the board
SPI-SCLK: P13.3; also elsewhere on the board

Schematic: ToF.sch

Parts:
C28: 4.7u; C_0402
C29: 0.1u; C_0201
P11: ToF_Host; STAND_PR_HOST
P12: ToF_Slave; STAND_PR_SLAVE
R23, R24: 4.7k; R_0201
U9: VL53L0X

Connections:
+3V3: P11.1; also elsewhere on the board
/ToF/s_3.3V: C28.1, C29.1, P12.1, R23.1, R24.1, U9.1 (AVDDVCSEL), U9.5 (XSHUT), U9.11 (AVDD)
/ToF/s_GND: C28.2, C29.2, P12.4, U9.2 (AVSSVCSEL), U9.3 (GND), U9.4 (GND2), U9.6 (GND3), U9.12 (GND4)
/ToF/s_SCL: P12.3, R24.2, U9.10 (SCL)
/ToF/s_SDA: P12.2, R23.2, U9.9 (SDA)
GND: P11.4; also elsewhere on the board
I2C-SCL: P11.3; also elsewhere on the board
I2C-SDA: P11.2; also elsewhere on the board

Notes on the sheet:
ToF

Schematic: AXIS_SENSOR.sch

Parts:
C31, C32: 0.1u; C_0201
U11: ICM-20602; LGA-16-3x3

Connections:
+3V3: C31.1, U11.1 (VDDIO), U11.16 (VDD); also elsewhere on the board
GND: C31.2, C32.2, U11.8 (FSYNC), U11.9 (RESV), U11.10 (RESV), U11.11 (RESV), U11.12 (RESV), U11.13 (GND), U11.15 (RESV); also elsewhere on the board
unnamed: C32.1, U11.14 (REGOUT)
SPI-CS-AXIS: U11.5 (CS); also elsewhere on the board
SPI-MISO: U11.4 (SA0/SDO); also elsewhere on the board
SPI-MOSI: U11.3 (SDA/SDI); also elsewhere on the board
SPI-SCLK: U11.2 (SCL/SPC); also elsewhere on the board

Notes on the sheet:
AXIS Sensor

Board: 2 copper layers, 130 parts (32 on the bottom side), 111 nets, no tracks yet.

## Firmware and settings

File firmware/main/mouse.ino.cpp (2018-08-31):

/**
 * @file    mouse.ino.cpp
 * @author  KERI (Github: kerikun11)
 * @date    2017.10.25
 */

#include "global.h"
#include <SPIFFS.h>
#include <WiFi.h>
#include <cstdio>
#include <iostream>
#include <sstream>

void mainTask(void *arg);
void printTask(void *arg);
void timeKeepTask(void *arg);
std::stringstream logstream;

void setup() {
  WiFi.mode(WIFI_OFF);
  for (auto p : CONFIG_SPI_CS_PINS)
    pinMode(p, INPUT_PULLUP);
  printf("\n**************** KERISE ****************\n");
  if (!bz.begin())
    bz.play(Buzzer::ERROR);
  if (!I2C::install(I2C_PORT_NUM, I2C_SDA_PIN, I2C_SCL_PIN))
    bz.play(Buzzer::ERROR);
  if (!led.begin())
    bz.play(Buzzer::ERROR);
  ui.batteryCheck();
  bz.play(Buzzer::BOOT);

  if (!SPIFFS.begin(true))
    bz.play(Buzzer::ERROR);
  if (!SPI::busInit(CONFIG_SPI_HOST, CONFIG_SPI_SCLK_PIN, CONFIG_SPI_MISO_PIN,
                    CONFIG_SPI_MOSI_PIN, CONFIG_SPI_DMA_CHAIN))
    bz.play(Buzzer::ERROR);
  if (!imu.begin(ICM20602_SPI_HOST, ICM20602_CS_PIN))
    bz.play(Buzzer::ERROR);
  if (!enc.begin(AS5048A_SPI_HOST, AS5048A_CS_PIN))
    bz.play(Buzzer::ERROR);
  if (!ref.begin())
    bz.play(Buzzer::ERROR);
  if (!tof.begin())
    bz.play(Buzzer::ERROR);
  if (!wd.begin())
    bz.play(Buzzer::ERROR);
  em.begin();

  xTaskCreate(printTask, "print", 4096, NULL, 1, NULL);
  // xTaskCreate(timeKeepTask, "TimeKeep", 4096, NULL, 1, NULL);
  xTaskCreate(mainTask, "main", 4096, NULL, 1, NULL);
}

void loop() { delay(1000); }

void printTask(void *arg) {
  portTickType xLastWakeTime = xTaskGetTickCount();
  while (1) {
    vTaskDelayUntil(&xLastWakeTime, 100 / portTICK_RATE_MS);
    // ref.csv();
    // tof.csv();
    // imu.print();
    // wd.print();
    // printf("%.1f,%.1f,%.1f,%.1f,%.1f,%.1f,%.1f\n", sc.target.trans,
    //        sc.actual.trans, sc.enconly.trans, sc.Kp * sc.proportional.trans,
    //        sc.Ki * sc.integral.trans, sc.Kd * sc.differential.trans,
    //        sc.Kp * sc.proportional.trans + sc.Ki * sc.integral.trans +
    //            sc.Kd * sc.differential.trans);
  }
}

void timeKeepTask(void *arg) {
  const int searchig_time_ms = 3 * 60 * 1000;
  while (millis() < searchig_time_ms)
    delay(1000);
  bz.play(Buzzer::LOW_BATTERY);
  ms.forceBackToStart();
  while (1)
    delay(1000);
}

#define TEST_END_REMAIN 6
#define TEST_ST_LOOK_AHEAD(v) (6 + v / 100)
#define TEST_ST_FB_GAIN 10
#define TEST_ST_TR_FB_GAIN 0

void straight_x(const float distance, const float v_max, const float v_end) {
  const float a_max = 9000;
  const float v_start = sc.actual.trans;
  AccelDesigner ad(a_max, v_start, v_max, v_end, sc.position.x,
                   distance - TEST_END_REMAIN);
  portTickType xLastWakeTime = xTaskGetTickCount();
  for (float t = 0.0f; true; t += 0.001f) {
    Position cur = sc.position;
    //    if (cur.x > distance - TEST_END_REMAIN) break;
    if (t > ad.t_end())
      break;
    float velocity = ad.v(t) + TEST_ST_TR_FB_GAIN * (ad.x(t) - cur.x);
    float theta = atan2f(-cur.y, TEST_ST_LOOK_AHEAD(velocity)) - cur.theta;
    sc.set_target(velocity, TEST_ST_FB_GAIN * theta);
    //    wallAvoid();
    //    wallCut();
    vTaskDelayUntil(&xLastWakeTime, 1 / portTICK_RATE_MS);
    xLastWakeTime = xTaskGetTickCount();
  }
  sc.set_target(ad.v_end(), 0);
  //  updateOrigin(Position(distance, 0, 0));
}

void turn(const float angle) {
  const float speed = 3.6 * M_PI;
  const float accel = 36 * M_PI;
  const float decel = 36 * M_PI;
  const float back_gain = 1.0f;
  int ms = 0;
  portTickType xLastWakeTime = xTaskGetTickCount();
  while (1) {
    if (fabs(sc.actual.rot) > speed)
      break;
    float delta = sc.position.x * cos(-sc.position.theta) -
                  sc.position.y * sin(-sc.position.theta);
    if (angle > 0) {
      sc.set_target(-delta * back_gain, ms / 1000.0f * accel);
    } else {
      sc.set_target(-delta * back_gain, -ms / 1000.0f * accel);
    }
    vTaskDelayUntil(&xLastWakeTime, 1 / portTICK_RATE_MS);
    xLastWakeTime = xTaskGetTickCount();
    ms++;
  }
  while (1) {
    vTaskDelayUntil(&xLastWakeTime, 1 / portTICK_RATE_MS);
    xLastWakeTime = xTaskGetTickCount();
    float extra = angle - sc.position.theta;
    if (fabs(sc.actual.rot) < 0.1 && fabs(extra) < 0.1)
      break;
    float target_speed = sqrt(2 * decel * fabs(extra));
    float delta = sc.position.x * cos(-sc.position.theta) -
                  sc.position.y * sin(-sc.position.theta);
    target_speed = (target_speed > speed) ? speed : target_speed;
    if (extra > 0) {
      sc.set_target(-delta * back_gain, target_speed);
    } else {
      sc.set_target(-delta * back_gain, -target_speed);
    }
  }
  sc.set_target(0, 0);
  //  updateOrigin(Position(0, 0, angle));
  //  printPosition("Turn End");
}

void position_test() {
  if (!ui.waitForCover())
    return;
  led = 9;
  delay(1000);
  sc.enable();
  sc.set_target(0, 0);
  ui.waitForCover();
  sc.disable();
}

void accel_test() {
  if (!ui.waitForCover())
    return;
  delay(500);
  logstream.flush();
  auto printLog = []() {
    logstream << "0";
    logstream << "," << sc.target.trans;
    logstream << "," << sc.actual.trans;
    logstream << "," << sc.enconly.trans;
    logstream << "," << sc.Kp * sc.proportional.trans;
    logstream << "," << sc.Ki * sc.integral.trans;
    logstream << "," << sc.Kd * sc.differential.trans;
    logstream << ","
              << sc.Kp * sc.proportional.trans + sc.Ki * sc.integral.trans +
                     sc.Kd * sc.differential.trans;
    logstream << std::endl;
  };
  imu.calibration();
  fan.drive(0.4);
  delay(500);
  sc.enable();
  const float accel = 6000;
  const float v_max = 1200;
  AccelDesigner ad(accel, 0, v_max, 0, 90 * 4);
  portTickType xLastWakeTime = xTaskGetTickCount();
  for (float t = 0; t < ad.t_end() + 0.2f; t += 0.001f) {
    sc.set_target(ad.v(t), 0);
    vTaskDelayUntil(&xLastWakeTime, 1 / portTICK_RATE_MS);
    xLastWakeTime = xTaskGetTickCount();
    printLog();
  }
  sc.set_target(0, 0);
  bz.play(Buzzer::CANCEL);
  sc.disable();
  fan.drive(0);
}

void turn_test() {
  if (!ui.waitForCover())
    return;
  delay(1000);
  imu.calibration();
  bz.play(Buzzer::CONFIRM);
  sc.enable();
  turn(-10 * 2 * PI);
  turn(10 * 2 * PI);
  sc.disable();
  bz.play(Buzzer::CANCEL);
}

void trapizoid_test() {
  if (!ui.waitForCover())
    return;
  delay(1000);
  imu.calibration();
  fan.drive(0.5);
  delay(500);
  sc.enable();
  const float accel = 15000;
  const float decel = 12000;
  const float v_max = 2400;
  const float v_start = 0;
  float T = 1.5f * (v_max - v_start) / accel;
  portTickType xLastWakeTime = xTaskGetTickCount();
  for (int ms = 0; ms / 1000.0f < T; ms++) {
    float velocity_a = v_start + (v_max - v_start) * 6.0f *
                                     (-1.0f / 3 * pow(ms / 1000.0f / T, 3) +
                                      1.0f / 2 * pow(ms / 1000.0f / T, 2));
    sc.set_target(velocity_a, 0);
    vTaskDelayUntil(&xLastWakeTime, 1 / portTICK_RATE_MS);
    xLastWakeTime = xTaskGetTickCount();
  }
  bz.play(Buzzer::SELECT);
  delay(150);
  bz.play(Buzzer::SELECT);
  for (float v = v_max; v > 0; v -= decel / 1000) {
    sc.set_target(v, 0);
    delay(1);
  }
  sc.set_target(0, 0);
  delay(150);
  bz.play(Buzzer::CANCEL);
  sc.disable();
  fan.drive(0);
}

void straight_test() {
  if (!ui.waitForCover())
    return;
  delay(1000);
  bz.play(Buzzer::SELECT);
  imu.calibration();
  sc.enable();
  fan.drive(0.5);
  delay(500);
  sc.position.x = 0;
  straight_x(12 * 90 - 3 - MACHINE_TAIL_LENGTH, 2400, 0);
  sc.set_target(0, 0);
  delay(100);
  fan.drive(0);
  delay(500);
  sc.disable();
}

void log_test() {
  if (!ui.waitForCover())
    return;
  delay(1000);
  logstream.flush();
  auto printLog = []() {
    logstream << enc.position(0) << ",";
    logstream << enc.position(1) << ",";
    logstream << imu.gyro.z << ",";
    logstream << imu.accel.y << ",";
    logstream << std::endl;
  };
  bz.play(Buzzer::SELECT);
  imu.calibration();
  bz.play(Buzzer::CANCEL);
  portTickType xLastWakeTime = xTaskGetTickCount();
  for (int i = 0; i < 500; i++) {
    mt.drive(i, i);
    printLog();
    vTaskDelayUntil(&xLastWakeTime, 1 / portTICK_RATE_MS);
  }
  mt.drive(0, 0);
  vTaskDelay(500 / portTICK_RATE_MS);
  mt.free();
}

void petitcon() {
  if (!ui.waitForCover())
    return;
  delay(500);
  //      fr.set_path("sssssssrlrlrlrlrlrlssssslrlrlrlrlrlrsssssrlrlrlrlrlrssssssssrlrlrlrlrsssssssssssssssslrlrlrlrlsssssssslrlrlrlrlssssslrlrlrlrlrlrsssssrlrlrlrlrlrlssssss");
  fr.set_path("sssssssrlrlrlrlrlrlssssslrlrlrlrlrlrsssssrlrlrlrlrlrssssssssrl"
              "rlrlrlrlrssssssssssssssssssslrlrlrlrlrlsssssssslrlrlrlrlrlssss"
              "slrlrlrlrlrlrsssssrlrlrlrlrlrlssssss");
  //      fr.set_path("ssssssssrlrrlrssssssss");
  imu.calibration();
  fr.enable();
  fr.waitForEnd();
  fr.disable();
}

void normal_drive() {
  int mode = ui.waitForSelect(16);
  switch (mode) {
  //* 走行
  case 0:
    bz.play(Buzzer::SUCCESSFUL);
    if (!ui.waitForCover())
      return;
    led = 9;
    ms.start();
    btn.flags = 0;
    while (ms.isRunning() && !btn.pressed)
      delay(100);
    delay(1000);
    bz.play(Buzzer::CANCEL);
    btn.flags = 0;
    ms.terminate();
    break;
  //* 走行パラメータの選択 & 走行
  case 1: {
    int preset = ui.waitForSelect(16);
    if (preset < 0)
      return;
    switch (preset) {
    case 0: fr.runParameter = FastRun::RunParameter(0.7, 1200, 3000, 3000); break;
    case 1: fr.runParameter = FastRun::RunParameter(0.7, 1500, 3600, 3600); break;
    case 2: fr.runParameter = FastRun::RunParameter(0.7, 1800, 4500, 4500); break;
    case 3: fr.runParameter = FastRun::RunParameter(0.7, 2100, 6000, 6000); break;
    case 4: fr.runParameter = FastRun::RunParameter(0.8, 1200, 3000, 3000); break;
    case 5: fr.runParameter = FastRun::RunParameter(0.8, 1500, 3600, 3600); break;
    case 6: fr.runParameter = FastRun::RunParameter(0.8, 1800, 4500, 4500); break;
    case 7: fr.runParameter = FastRun::RunParameter(0.8, 2100, 6000, 6000); break;
    case 8: fr.runParameter = FastRun::RunParameter(0.9, 1200, 3000, 3000); break;
    case 9: fr.runParameter = FastRun::RunParameter(0.9, 1500, 3600, 3600); break;
    case 10: fr.runParameter = FastRun::RunParameter(0.9, 1800, 4500, 4500); break;
    case 11: fr.runParameter = FastRun::RunParameter(0.9, 2100, 6000, 6000); break;
    case 12: fr.runParameter = FastRun::RunParameter(1.0, 1200, 3000, 3000); break;
    case 13: fr.runParameter = FastRun::RunParameter(1.0, 1500, 3600, 3600); break;
    case 14: fr.runParameter = FastRun::RunParameter(1.0, 1800, 4500, 4500); break;
    case 15: fr.runParameter = FastRun::RunParameter(1.0, 2100, 6000, 6000); break;
    }
  }
    bz.play(Buzzer::SUCCESSFUL);
    break;
  //* 速度の設定
  case 2: {
    int value;
    for (int i = 0; i < 1; i++)
      bz.play(Buzzer::SHORT);
    value = ui.waitForSelect(16);
    if (value < 0)
      return;
    const float curve_gain = 0.1f * value;
    for (int i = 0; i < 2; i++)
      bz.play(Buzzer::SHORT);
    value = ui.waitForSelect(16);
    if (value < 0)
      return;
    const float v_max = 300.0f * value;
    for (int i = 0; i < 3; i++)
      bz.play(Buzzer::SHORT);
    value = ui.waitForSelect(16);
    if (value < 0)
      return;
    const float accel = 1000.0f * value;
    fr.runParameter = FastRun::RunParameter(curve_gain, v_max, accel, accel);
  }
    bz.play(Buzzer::SUCCESSFUL);
    break;
  //* 壁制御の設定
  case 3: {
    int value = ui.waitForSelect(16);
    if (value < 0)
      return;
    fr.wallAvoidFlag = value & 0x01;
    fr.wallAvoid45Flag = value & 0x02;
    fr.wallCutFlag = value & 0x04;
    fr.V90Enabled = value & 0x08;
  }
    bz.play(Buzzer::SUCCESSFUL);
    break;
  //* ファンの設定
  case 4: {
    fan.drive(fr.fanDuty);
    delay(100);
    fan.drive(0);
    int value = ui.waitForSelect(11);
    if (value < 0)
      return;
    fr.fanDuty = 0.1f * value;
    fan.drive(fr.fanDuty);
    ui.waitForSelect(1);
    fan.drive(0);
  }
    bz.play(Buzzer::SUCCESSFUL);
    break;
  //* 宴会芸
  case 5:
    position_test();
    break;
  //* 迷路データの復元
  case 7:
    bz.play(Buzzer::MAZE_RESTORE);
    if (!ms.restore()) {
      bz.play(Buzzer::ERROR);
      return;
    }
    bz.play(Buzzer::SUCCESSFUL);
    break;
  //* 前壁キャリブレーション
  case 8:
    led = 6;
    if (!ui.waitForCover(true))
      return;
    delay(1000);
    bz.play(Buzzer::CONFIRM);
    wd.calibrationFront();
    bz.play(Buzzer::CANCEL);
    break;
  //* 横壁キャリブレーション
  case 9:
    led = 9;
    if (!ui.waitForCover())
      return;
    delay(1000);
    bz.play(Buzzer::CONFIRM);
    wd.calibrationSide();
    bz.play(Buzzer::CANCEL);
    break;
  //* 前壁補正データの保存
  case 10:
    if (!ui.waitForCover())
      return;
    if (wd.backup()) {
      bz.play(Buzzer::SUCCESSFUL);
    } else {
      bz.play(Buzzer::ERROR);
    }
    break;
  //* ゴール区画の設定
  case 11: {
    for (int i = 0; i < 2; i++)
      bz.play(Buzzer::SHORT);
    int value = ui.waitForSelect(4);
    if (value < 0)
      return;
    switch (value) {
    case 0: {
      int x = ui.waitForSelect(16);
      int y = ui.waitForSelect(16);
      ms.set_goal({Vector(x, y)});
      break;
    }
    case 1:
      ms.set_goal({Vector(1, 0)});
      break;
    case 2:
      ms.set_goal({Vector(4, 4), Vector(4, 5), Vector(5, 4), Vector(5, 5)});
      break;
    case 3:
      ms.set_goal({Vector(15, 15)});
      break;
    }
    bz.play(Buzzer::SUCCESSFUL);
  } break;
  //* マス直線
  case 12:
    if (!ui.waitForCover(true))
      return;
    delay(1000);
    bz.play(Buzzer::CONFIRM);
    imu.calibration();
    bz.play(Buzzer::CANCEL);
    sc.enable();
    straight_x(9 * 90 - 6 - MACHINE_TAIL_LENGTH, 300, 0);
    sc.disable();
    break;
    //* テスト
  case 13:
    // log_test();
    // trapizoid_test();
    accel_test();
    // straight_test();
    // petitcon();
    break;
  //* ログの表示
  case 14:
    std::cout << logstream.str();
    break;
  //* リセット
  case 15:
    ms.print();
    ESP.restart();
    break;
  }
}

void mainTask(void *arg) {
  while (1) {
    normal_drive();
    delay(1);
  }
}

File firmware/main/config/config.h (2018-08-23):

#pragma once

/* Hardware Mapping */
#define BAT_VOL_PIN 35
#define PR_TX_PINS                                                             \
  { 12, 13, 12, 13 }
#define PR_RX_PINS                                                             \
  { 36, 38, 39, 37 }
#define BUTTON_PIN GPIO_NUM_0
#define LED_PINS                                                               \
  { 2, 4, 5, 27 }

/* SPI Bus*/
#define CONFIG_SPI_MOSI_PIN GPIO_NUM_23
#define CONFIG_SPI_MISO_PIN GPIO_NUM_19
#define CONFIG_SPI_SCLK_PIN GPIO_NUM_18
#define CONFIG_SPI_HOST HSPI_HOST
#define CONFIG_SPI_DMA_CHAIN 0

/* SPI Device */
#define AS5048A_SPI_HOST CONFIG_SPI_HOST
#define AS5048A_CS_PIN GPIO_NUM_15

#define ICM20602_SPI_HOST CONFIG_SPI_HOST
#define ICM20602_CS_PIN GPIO_NUM_14

/* for pull-up*/
#define CONFIG_SPI_CS_PINS                                                     \
  { AS5048A_CS_PIN, ICM20602_CS_PIN }

/* I2C Bus*/
#define I2C_SDA_PIN GPIO_NUM_21
#define I2C_SCL_PIN GPIO_NUM_22
#define I2C_PORT_NUM I2C_NUM_0

/* I2C Device */
#define I2C_PORT_NUM_TOF I2C_PORT_NUM

/* LED Controller */
#define MOTOR_L_CTRL1_PIN 25 // 16
#define MOTOR_L_CTRL2_PIN 26 // 17
#define MOTOR_R_CTRL1_PIN 16 // 25
#define MOTOR_R_CTRL2_PIN 17 // 26

#define FAN_PIN 33

#define BUZZER_PIN 32

#define LEDC_CH_MOTOR_L_CTRL1 0
#define LEDC_CH_MOTOR_L_CTRL2 1
#define LEDC_CH_MOTOR_R_CTRL1 2
#define LEDC_CH_MOTOR_R_CTRL2 3

#define LEDC_CH_FAN 6

#define LEDC_CH_BUZZER 4

/* Machine Size Parameter */
#define MACHINE_ROTATION_RADIUS 16.75f
#define MACHINE_GEAR_RATIO (13.0f / 41.0f)
#define MACHINE_WHEEL_DIAMETER 13.807967f
#define MACHINE_TAIL_LENGTH 18.4f

/* Field Size Parameter */
#define SEGMENT_WIDTH 90.0f
#define SEGMENT_DIAGONAL_WIDTH 127.2792206135786f
#define WALL_THICKNESS 6.0f

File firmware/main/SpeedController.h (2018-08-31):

#pragma once

#include "Accumulator.h"
#include <cmath>

#include "motor.h"
extern Motor mt;
#include "imu.h"
extern IMU imu;
#include "encoder.h"
extern Encoder enc;

class Position {
public:
  float x, y, theta;

public:
  Position(const float x = 0, const float y = 0, const float theta = 0)
      : x(x), y(y), theta(theta) {}
  Position(const float pos[3]) : x(pos[0]), y(pos[1]), theta(pos[2]) {}

  void reset() {
    x = 0;
    y = 0;
    theta = 0;
  }
  void set(const float x = 0, const float y = 0, const float theta = 0) {
    this->x = x;
    this->y = y;
    this->theta = theta;
  }
  const Position rotate(const float angle) const {
    return Position(x * cos(angle) - y * sin(angle),
                    x * sin(angle) + y * cos(angle), theta);
  }
  float getNorm() const { return sqrt(x * x + y * y); }
  Position mirror_x() const { return Position(x, -y, -theta); }

  Position operator=(const Position &obj) {
    x = obj.x;
    y = obj.y;
    theta = obj.theta;
    return *this;
  }
  Position operator+() const { return Position(x, y, theta); }
  Position operator+(const Position &obj) const {
    return Position(x + obj.x, y + obj.y, theta + obj.theta);
  }
  Position operator+=(const Position &obj) {
    x += obj.x;
    y += obj.y;
    theta += obj.theta;
    return *this;
  }
  Position operator-() const { return Position(-x, -y, -theta); }
  Position operator-(const Position &obj) const {
    return Position(x - obj.x, y - obj.y, theta - obj.theta);
  }
  Position operator-=(const Position &obj) {
    x -= obj.x;
    y -= obj.y;
    theta -= obj.theta;
    return *this;
  }
  inline void print(const char *name = "Pos") {
    printf("%s: (%.1f,\t%.1f,\t%.3f)\n", name, x, y, theta);
  }
};

#define SPEED_CONTROLLER_TASK_PRIORITY 4
#define SPEED_CONTROLLER_STACK_SIZE 4096

#define SPEED_CONTROLLER_KP 1.2f
#define SPEED_CONTROLLER_KI 144.0f
#define SPEED_CONTROLLER_KD 0.01f

#define SPEED_CONTROLLER_PERIOD_US 1000

class SpeedController {
public:
  struct WheelParameter {
  public:
    float trans;    //< translation [mm]
    float rot;      //< rotation [rad]
    float wheel[2]; //< wheel position [mm], wheel[0]:left, wheel[1]:right
  public:
    WheelParameter() {}
    void pole2wheel() {
      wheel[0] = trans - MACHINE_ROTATION_RADIUS * rot;
      wheel[1] = trans + MACHINE_ROTATION_RADIUS * rot;
    }
    void wheel2pole() {
      rot = (wheel[1] - wheel[0]) / 2 / MACHINE_ROTATION_RADIUS;
      trans = (wheel[1] + wheel[0]) / 2;
    }
    void clear() {
      trans = 0;
      rot = 0;
      wheel[0] = 0;
      wheel[1] = 0;
    }
  };
  WheelParameter target;
  WheelParameter actual;
  WheelParameter enconly;
  WheelParameter acconly;
  WheelParameter proportional;
  WheelParameter integral;
  WheelParameter differential;
  float Kp = SPEED_CONTROLLER_KP;
  float Ki = SPEED_CONTROLLER_KI;
  float Kd = SPEED_CONTROLLER_KD;
  Position position;
  int ave_num;

public:
  SpeedController() {
    enabled = false;
    reset();
    xTaskCreate([](void *obj) { static_cast<SpeedController *>(obj)->task(); },
                "SpeedController", SPEED_CONTROLLER_STACK_SIZE, this,
                SPEED_CONTROLLER_TASK_PRIORITY, NULL);
  }
  void enable(const bool &reset_position = true) {
    reset();
    if (reset_position)
      position.reset();
    enabled = true;
    printf("Speed Controller Enabled\n");
  }
  void disable() {
    enabled = false;
    delay(2);
    mt.free();
    printf("Speed Controller disabled\n");
  }
  void set_target(const float &trans, const float &rot) {
    target.trans = trans;
    target.rot = rot;
    target.pole2wheel();
  }

private:
  bool enabled = false;
  static const int acc_num = 16;
  Accumulator<float, acc_num> wheel_position[2];
  Accumulator<float, acc_num> accel;
  Accumulator<float, acc_num> gyro;
  WheelParameter actual_prev;
  WheelParameter target_prev;

  void reset() {
    target.clear();
    actual.clear();
    integral.clear();
    differential.clear();
    actual_prev.clear();
    target_prev.clear();
    for (int i = 0; i < 2; i++)
      wheel_position[i].clear(enc.position(i));
    accel.clear(imu.accel.y);
    gyro.clear(imu.gyro.z);
  }
  void task() {
    portTickType xLastWakeTime = xTaskGetTickCount();
    while (1) {
      vTaskDelayUntil(&xLastWakeTime, 1 / portTICK_RATE_MS);
      xLastWakeTime = xTaskGetTickCount();
      if (enabled == false)
        continue; //< 有効でなければスルー

      // サンプリング終了まで待つ
      enc.samplingSemaphoreTake();
      imu.samplingSemaphoreTake();

      // 最新のデータの追加
      for (int i = 0; i < 2; i++)
        wheel_position[i].push(enc.position(i));
      accel.push(imu.accel.y);
      gyro.push(imu.gyro.z);

      // LPFのサンプル数を指定
      //        ave_num = std::min(acc_num, static_cast<int>(PI *
      //        MACHINE_GEAR_RATIO * MACHINE_WHEEL_DIAMETER / ((1.0f +
      //        fabs(target.trans)) * SPEED_CONTROLLER_PERIOD_US / 1000000)));
      ave_num = acc_num;

      float sum_accel = 0.0f;
      for (int j = 0; j < ave_num - 1; j++)
        sum_accel += accel[j];

      for (int i = 0; i < 2; i++) {
        actual.wheel[i] =
            (wheel_position[i][0] - wheel_position[i][ave_num - 1]) /
            (ave_num - 1) * 1000000 / SPEED_CONTROLLER_PERIOD_US;
        enconly.wheel[i] = (wheel_position[i][0] - wheel_position[i][1]) *
                           1000000 / SPEED_CONTROLLER_PERIOD_US;
      }
      acconly.trans = sum_accel * SPEED_CONTROLLER_PERIOD_US / 1000000 / 2;
      enconly.wheel2pole();

      // calculate actual value
      actual.wheel2pole();
      actual.trans += sum_accel * SPEED_CONTROLLER_PERIOD_US / 1000000 / 2;
      actual.rot = imu.gyro.z;
      actual.pole2wheel();

      // calculate pid value
      for (int i = 0; i < 2; i++) {
        integral.wheel[i] += (target.wheel[i] - actual.wheel[i]) *
                             SPEED_CONTROLLER_PERIOD_US / 1000000;
        proportional.wheel[i] = target.wheel[i] - actual.wheel[i];
      }
      integral.wheel2pole();
      proportional.wheel2pole();
      differential.trans = (target.trans - target_prev.trans) /
                               SPEED_CONTROLLER_PERIOD_US * 1000000 -
                           accel[0];
      //        differential.rot = (target.rot - target_prev.rot) /
      //        SPEED_CONTROLLER_PERIOD_US * 1000000 - imu.angular_accel;
      differential.rot =
          (target.rot - target_prev.rot) / SPEED_CONTROLLER_PERIOD_US *
              1000000 -
          (gyro[0] - gyro[1]) / SPEED_CONTROLLER_PERIOD_US * 1000000;
      differential.pole2wheel();
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

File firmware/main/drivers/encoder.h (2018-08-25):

#pragma once

#include <driver/spi_master.h>
#include <esp_err.h>

#define ENCODER_PULSES 16384

#define ENCODER_STACK_SIZE 4096
#define ENCODER_PRIORITY 5

class Encoder {
public:
  Encoder() { sampling_end_semaphore = xSemaphoreCreateBinary(); }
  bool begin(spi_host_device_t spi_host, int8_t pin_cs) {
    // ESP-IDF SPI device initialization
    static spi_device_interface_config_t dev_cfg;
    dev_cfg.command_bits = 1;
    dev_cfg.address_bits = 0;
    dev_cfg.dummy_bits = 0;
    dev_cfg.mode = 1;
    dev_cfg.duty_cycle_pos = 0;
    dev_cfg.cs_ena_pretrans = 0;
    dev_cfg.cs_ena_posttrans = 0;
    dev_cfg.clock_speed_hz = 10000000;
    dev_cfg.spics_io_num = pin_cs;
    dev_cfg.flags = 0;
    dev_cfg.queue_size = 1;
    dev_cfg.pre_cb = NULL;
    dev_cfg.post_cb = NULL;
    ESP_ERROR_CHECK(spi_bus_add_device(spi_host, &dev_cfg, &encoder_spi));
    xTaskCreate([](void *obj) { static_cast<Encoder *>(obj)->task(); },
                "Encoder", ENCODER_STACK_SIZE, this, ENCODER_PRIORITY, NULL);
    return true;
  }
  float position(uint8_t ch) {
    float value = ((float)pulses_ovf[ch] * ENCODER_PULSES + pulses[ch]) *
                  MACHINE_WHEEL_DIAMETER * M_PI * MACHINE_GEAR_RATIO /
                  ENCODER_PULSES;
    if (ch == 1)
      value = -value;
    return value;
  }
  int getPulses(uint8_t ch) {
    int value = pulses_ovf[ch] * ENCODER_PULSES + pulses[ch];
    if (ch == 1)
      value = -value;
    return value;
  }
  int getRaw(uint8_t ch) {
    int value = pulses[ch];
    if (ch == 1)
      value = -value;
    return value;
  }
  void print() { log_d("Encoder L:\t%f\tR:\t%f\n", position(0), position(1)); }
  void csv() {
    //      printf("0,%d,%d,%d,%d\n", ENCODER_PULSES, -ENCODER_PULSES,
    //      getRaw(0), getRaw(1)); printf("0,%d,%d,%d,%d\n", ENCODER_PULSES,
    //      -ENCODER_PULSES, getPulses(0), getPulses(1));
    printf("0,%f,%f\n", position(0), position(1));
  }
  void samplingSemaphoreTake(portTickType xBlockTime = portMAX_DELAY) {
    xSemaphoreTake(sampling_end_semaphore, xBlockTime);
  }

private:
  spi_device_handle_t encoder_spi;
  SemaphoreHandle_t sampling_end_semaphore;
  int pulses[2];
  int pulses_prev[2];
  int pulses_ovf[2];

  void update() {
    uint8_t rxbuf[4];
    static spi_transaction_t tx;
    tx.flags |= SPI_TRANS_USE_TXDATA;
    tx.tx_data[0] = 0xFF;
    tx.tx_data[1] = 0xFF;
    tx.tx_data[2] = 0xFF;
    tx.tx_data[3] = 0xFF;
    tx.rx_buffer = rxbuf;
    tx.length = 32;
    ESP_ERROR_CHECK(spi_device_transmit(encoder_spi, &tx));

    pulses[1] = ((uint16_t)(0x3F & (rxbuf[0])) << 8) | rxbuf[1];
    pulses[0] = ((uint16_t)(0x3F & (rxbuf[2])) << 8) | rxbuf[3];
    for (int i = 0; i < 2; i++) {
      if (pulses[i] > pulses_prev[i] + ENCODER_PULSES / 2) {
        pulses_ovf[i]--;
      } else if (pulses[i] < pulses_prev[i] - ENCODER_PULSES / 2) {
        pulses_ovf[i]++;
      }
      pulses_prev[i] = pulses[i];
    }
  }

  void task() {
    portTickType xLastWakeTime = xTaskGetTickCount();
    while (1) {
      vTaskDelayUntil(&xLastWakeTime, 1 / portTICK_RATE_MS);
      xLastWakeTime = xTaskGetTickCount();
      update();
      xSemaphoreGive(sampling_end_semaphore);
    }
  }
};

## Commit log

2017-09-15 KiCadファイルを追加
    KERISEv3-2 発注版
    [AXIS_SENSOR.sch, COM.sch, Encoder.sch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]
2017-09-15 フットプリントのミスを修正
    [KERISE.kicad_pcb]
2017-09-21 フットプリントを改良，アナログ電源を分離
    [IR_RCV.sch, KERISE.dsn, KERISE.kicad_pcb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]
2017-09-24 回路とフットプリントを改良
    [AXIS_SENSOR.sch, COM.sch, Encoder.sch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]
2017-09-24 各種機能テスト用ファームウェアを追加
2017-09-24 ギアのDXFファイルを追加
    [12.dxf, 12.stp, 13.dxf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]
2017-10-17 自動配線1残し
    [AXIS_SENSOR.sch, COM.sch, Encoder.sch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]
2017-10-17 自動配線を適用，ロゴを追加
    [KERISE.kicad_pcb]
2017-10-26 KERISEv3からファームウェアを移植，各種動作確認用プログラムを追加
    [KERISE.kicad_pcb]
2017-10-27 実装経験をもとにフットプリントを改良，ミスを修正
    SC70サイズのオペアンプのピンアサインを修正
    [AXIS_SENSOR.sch, COM.sch, Encoder.sch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]
2017-10-27 BLEの送信クラスを追加
2017-10-27 モーターとエンコーダの動作を確認
2017-10-27 KERISEv3のコードのMPUをICM，AS4145をAS5048Aに変更
2017-10-27 ToFとBLEのコードを追加
    未初期化
2017-10-28 複数デバイスで使用しているSPIバスの初期化をbeginの引数で選択するように変更
2017-10-28 mouseにToFとBLEを追加，未動作確認
2017-10-29 エンコーダの値が飛ぶバグを修正，ICM20602のキャリブレーション方法を改良
    AS5048AはSCLKがCSと同時に下がると1クロック目が失われる仕様がある．
    それを回避するために，CSをdigitalWrite()でやっていたが，これがICM20602との通信と衝突していた可能性がある．
    SPI前後のコールバック関数内でdigitalWrite()をすることで解決．
    ICM20602のキャリブレーションを2秒1回ではなく，500ms4回にすることで精度が飛躍的に向上
    [as5048a.h, config.h, icm20602.h]
2017-10-29 BLE.begin()でassertするバグを修正，ToFの読み値をBLEで送るコードの追加
    WiFi.mode(WIFI_OFF);が邪魔をしていた
2017-10-29 各種テストコードの移植，ジャイロの係数の更新
    機体を10周手で回して，角度の積算をみて係数を更新．結構違った．
2017-10-30 モーターの配線ミスをソフトで修正！！宴会芸でPIDチューニング
    モーターが左右逆に取り付けてあった．ピン定義を入れ替えて対応
2017-11-01 迷路をSPIFFSに保存するサンプルプログラム
2017-11-02 ジャイロの係数を間違えて加速度にかけていたミスを修正
2017-11-02 ICM-20602の内蔵ローパスフィルタを有効化
2017-11-02 モーターを回すとICMのジャイロにノイズが入るバグを特定したコード
2017-11-04 enabledフラグ周りを改良
2017-11-05 ICM-20602を交換してなんとか動作
2017-11-05 クラス名を一般化．型番ではなく役割に
    今後は役割にして，型番のドライバクラスを継承したい
2017-11-05 spi.inoのコードを更新
    AxisとEncoderに統一
2017-11-05 SPIピンの定義方法を変更
    デバイスごとに定義
2017-11-05 Mazeクラスを整理
2017-11-05 PIDチューニング，まあまあ
2017-11-06 ToFを追加
2017-11-06 最短でゴールについた後にクラッシュするバグを修正．
    vTaskDelayUntilは呼ばない間の分が連続で呼ばれることが分かった
2017-11-06 xLastWakeTimeの初期化を1行で行う
    見やすく
2017-11-06 ToFによる曲がる前の前壁補正
2017-11-07 ESP32のPreferemcesに前壁パラメータを保存
2017-11-07 壁切れの実装，前壁補正，割といい感じ
2017-11-08 前壁キャリブレーション機能を追加
2017-11-08 横壁補正を調整，ちょっといい感じ．
    最短にも横壁補正を入れた．
    壁切れはエラーが多いので一時停止
2017-11-08 ゲイン調整，なんとか動いた
2017-11-11 横壁補正のゲインを一定に．
2017-11-12 車輪の径を更新，最短に壁切れを追加，Position::rotate()の仕様変更
2017-11-13 インターフェースを更新，最短走行の壁制御を選択できるように
2017-11-13 横壁制御に飽和を追加，いい感じ
2017-11-13 横壁制御を端的なものに復帰
2017-11-14 utils.hファイルを一時的に作成
    コードを見やすく
2017-11-14 utils.cppを作成
    ヘッダファイルにCコードを書くのはよくない
2017-11-14 軌道を改良
    最新の直観に基づく
2017-11-14 軌道のバグ修正
    配列の個数の定義を間違えていた
2017-11-16 複数区画がゴールだとAgent::reset()したときにREACHED_START状態にならないバグを修正
2017-11-16 最新の探索器に更新
2017-11-16 最短走行に小回り90度を追加，斜めなしモード
    斜め走行がないモードを生成
2017-11-16 最短小回り90度の軌道生成コードを追加
2017-11-16 直線制御の終端速度を関数を抜けるタイミングで達成できるように変更
2017-11-17 全日本前日パラメータ
2017-11-18 ファンの回転数を変える機能を搭載
2017-11-18 ハーフ決勝用にゴールと時間を設定
2017-11-18 ゴールと探索終了時に一度止まって迷路をSPIFFSに保存
2017-11-18 横壁キャリブレーションはスタート時にせず，あらかじめ行っておくように変更
2017-11-18 前壁補正，ターン，既知区間スピードの調整
2017-11-19 全日本マイクロマウス2016パラメータ
2017-11-24 ログファイルを追加
2017-11-24 ゴール区画座標を練習用へ変更
2017-11-29 3Dモデルを追加
    TEPとFusion360ファイルの両方をエクスポート
    [bearing_1.5_4_2 v1.f3d, bearing_1.5_4_2 v1.step, bearing_2_5_2.5 v1.f3d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]
2017-12-01 ToFの測定コードを改良
    測定に失敗したときはpassed_msをクリアしない
2017-12-01 FastRunのターンにフィードフォワード項を入れて高速化
2017-12-04 AxisをIMUに名前変更
2017-12-04 debug.h を ExternalController.hに変更
2017-12-04 依存関係の整理
    不要なincludeを削除
    UserInterface.hの分割
2017-12-04 UserInterface.hを新たに生成
    マウスが持つあらゆるセンサを活用したUI
2017-12-04 探索のターンにもフィードフォワード項を追加
    探索スピードを上げることができた
2017-12-06 壁制御の調整
2017-12-07 壁センサの基準値保存をPreferencesではなくSPIFFSに保存
    管理をしやすくするため
2017-12-07 速度コントローラのコードを改良
    Accumulatorクラスを作成
2017-12-11 スタート時に前壁を作るバグを修正
    スタート前が直線のときToFの計測ができず，古いデータにより前壁ができていた．
2017-12-11 斜めの壁切れを導入
2017-12-11 スタート時に前壁を作るバグの再修正
    別のアプローチ
2017-12-22 プチコン用にスピードを調整
2018-01-01 機体を振ってモード選択する機能を実装
2018-01-07 新しいTaskBaseを導入
2018-01-09 TaskBaseを更新
    要動作確認！
2018-01-10 加速度の単位を修正
2018-01-10 グローバル変数の宣言をglobal.cppに集約
    global.cpp
    global.h
    を新規作成し，グローバル変数を管理
    ライブラリをよりライブラリらしくした
2018-01-14 リフレクタのバグを修正
    飽和の方向が間違っていた
2018-01-21 RTOSのスタックサイズと優先度をマクロで定義
    他のコードと統一的に
2018-01-23 エンコーダ偏心補正の実験コードを追加
    [data.csv]
2018-03-01 小さな改良
2018-03-28 SPIFFSへの書き込みに時間がかかるので，待つ．
2018-04-01 直線加速の新探索アルゴリズムを適用
2018-04-01 TaskBaseのバグを修正
2018-04-01 移動中に計算処理を行う新探索アルゴリズムを適用
2018-04-02 パラメータの調整
2018-04-03 迷路のバックアップ方式を変更，ログを残す
2018-04-03 バックアップコードを改良
2018-04-04 パラメータ調整
2018-04-04 袋小路でバックアップ
2018-04-05 動作確認用のコードを最新のmouseを基に更新
2018-04-05 Accumulator.hを導入
2018-04-05 軌道を更新
    [data.csv]
2018-04-05 KERISEv5の変更点を反映
2018-04-08 xLastWakeTimeの更新位置を変更
2018-04-08 Agent.hを導入
2018-04-12 ゴール区画を設定する機能
2018-04-13 宴会芸モードを追加
2018-04-15 曲線減速の導入，未完成
2018-04-17 AccelDesignerを追加
2018-04-18 MazeLibのバグを修正
2018-04-20 曲線デザイナを追加
2018-04-25 コードを改良
2018-04-25 cbrtのバグを修正
2018-04-26 コメントを改良
2018-05-01 calcVelocityEnd()のバグを修正
2018-05-25 MazeLibのcalcNextDirs()を更新
2018-05-26 第2回プチコンコード
2018-07-13 I2CをESP-IDFのものに変更
2018-08-17 strict char case
2018-08-22 ESP-IDFに移行，未動作確認
2018-08-22 add arduino config
2018-08-22 srcをフォルダ分け
2018-08-23 i2c.h および spi.h を導入
2018-08-25 rm Logger, format, fail safe
    [FastRun.h, SearchRun.h, SpeedController.h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]
2018-08-25 update WallDetector format and distance, fix warnnigs
    [FastRun.h, SearchRun.h, SpeedController.h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]
2018-08-30 ToFの接触不良を修正
2018-08-31 速度を早めたらなんか動いた
2018-09-01 探索速度を調整 東日本地区大会2018
2018-09-02 練習用ゴールに設定
2021-01-11 update directory structure
    [12.dxf, 12.stp, 13.dxf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]
